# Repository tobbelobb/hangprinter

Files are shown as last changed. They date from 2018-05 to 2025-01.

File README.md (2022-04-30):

Hangprinter Hangprinter logo
===========

Welcome to the Hangprinter repository!

This branch contains Hangprinter version 4.
Breaking changes might occur from time to time.

For more general information about the Hangprinter Project, refer to [hangprinter.org](https://hangprinter.org).

Documentation
----------------
Start here: [hangprinter.org/doc/v4](https://hangprinter.org/doc/v4/).

Using letter sized paper for the layout?
-------------------------
You can specify that in a make-call:
```
make layout_letter.pdf
```

The `make` call will require Cairosvg, sed, and Ghostscript to work.
Already installed on many standard GNU/Linux systems.

Contributing Improvements
-------------------------
We're super grateful for merge request.
Please submit to this repo on Gitlab.

The second best option for contributing improvements is to make an issue on Gitlab.

Lead Dev
---------------------------------
[tobben](https://torbjornludvigsen.com).

Campaign
---------------------------------
[Github Sponsors](https://github.com/sponsors/tobbelobb/)

Merchandise
---------------------------------
[Spreadshirt link for Sweden](https://shop.spreadshirt.se/hangprinter-merchandise/).
[Spreadshirt link for US](https://shop.spreadshirt.com/hangprinter-merchandise/).

Credits
-------
See [contributors](https://gitlab.com/tobben/hangprinter/graphs/version_4) for committer stats.
Note that almost all ideas implemented by the commits have come up in conversations among fellow Reprappers.
Thanks!

List sorted alphabetically.

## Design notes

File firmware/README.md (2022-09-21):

## State of Hangprinter v4 firmware as of Sep 21, 2022

HP4 uses stock RepRapFirmware and ODrive firmware.

Read the the config files closely, they provide the most detail about how to use HP4 firmware.

## Changelog

### Sep 21, 2022
Latest stock ODrivefirmware (v0.5.5) is now used by HP4.
No more old or custom ODrive firmwares.

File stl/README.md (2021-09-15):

Make individual stls on your own by
 * Opening up the scad-files with OpenSCAD GUI and exporting from there

Or with `make`
 * `make stl/<thefileyouwant.stl>`
 * `make <thefileyouwant.stl>`,

... which will both place the stl inside the `hangprinter/stl/` directory.

Make all the stls on your own by
 * `make all` (this will take a long time),

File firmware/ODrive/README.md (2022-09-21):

## ODrive Usage On Hangprinter

Hangprinter uses stock ODrive Firmware version 0.5.5 or later.

Use a <a href="https://odriverobotics.com/shop/usb-isolator">USB isolator</a> between your laptop and your ODrive.

The source is kept here:
[https://github.com/madcowswe/ODrive](github.com/madcowswe/ODrive).

[The official ODrive docs](https://docs.odriverobotics.com/v/0.5.5/getting-started.html) are helpful in explaining many of the commands.

### How to Configure

Read every line of `configure_odrive.py`, including the comments manually before executing any of them.
Most of it can be copy/pasted in blocks, but in some places you have to wait.

I've included config dumps of my own ODrives here, and it might be tempting to use upload them directly to your own ODrives, like this

```
$ odrivetool restore-config odrive-config-AB.json  # With AB ODrive connected
$ odrivetool restore-config odrive-config-CD.json  # With CD ODrive connected
```

After those commands, you need to confirm that your break resistance matches the configured one.
You also need to do a calibration sequence and set a couple of variables:
odrivetool:
```
odrv0.config.brake_resistance = your_measured_value
odrv0.axis0.requested_state = AXIS_STATE_FULL_CALIBRATION_SEQUENCE
# wait...
odrv0.axis1.requested_state = AXIS_STATE_FULL_CALIBRATION_SEQUENCE
# wait...
odrv0.axis0.encoder.config.pre_calibrated = True
odrv0.axis1.encoder.config.pre_calibrated = True
odrv0.axis0.requested_state = AXIS_STATE_IDLE
odrv0.axis1.requested_state = AXIS_STATE_IDLE
odrv0.save_configuration()
# wait...
```

Also, the config backup does not include anti-cogging, so you have to set that up separately.
Look into `config_odrive.py` for how I set up anti-cogging.

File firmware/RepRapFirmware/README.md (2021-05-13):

The RepRapFirmware published here is to help those who intend to help develop it.
The final Hangprinter v4 Prototype 2 and onwards will use stock ReprapFirmware.

## Duet3 Firmware
Is under development, and development binaries will be uploaded here from time to time.
There are no guarantees here that the binaries uploaded here are tested, or will work
for you in any particular way.
Use only if you know what you're doing.

Stock ReprapFirmware, that will be part of Hangprinter long term, is developed here:
https://github.com/Duet3D/RepRapFirmware/

## Duet2 Firmware
This one was used by the Hangprinter 4 Prototype 1.
It used a Duet2 (Wifi) board and custom firmware.
It is deprecated and should not be used.
The source is kept here:
https://github.com/tobbelobb/RepRapFirmware/tree/v2-dev_hangprinter

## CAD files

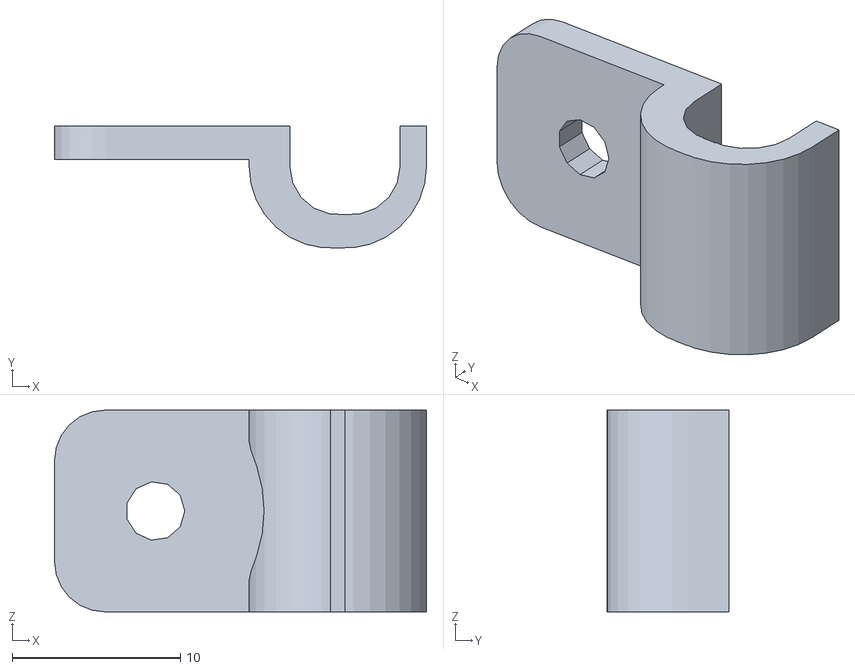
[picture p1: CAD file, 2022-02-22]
stl/cable_clamp_encoder_and_mains_cables.stl
22.1 x 7.27 x 12.0

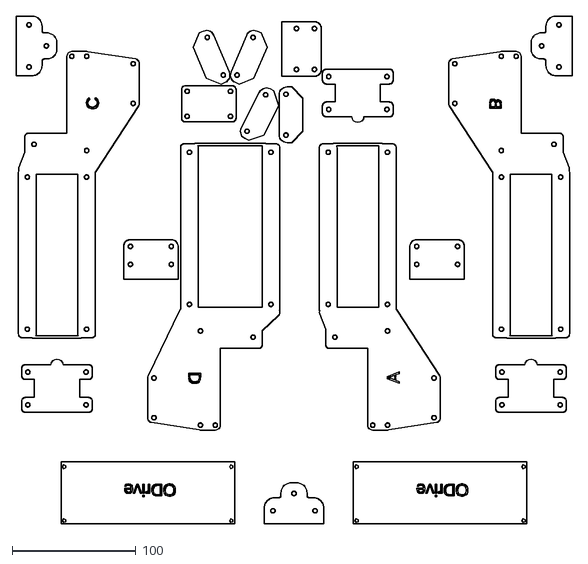
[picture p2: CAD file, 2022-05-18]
layout.dxf
448.7 x 409.7

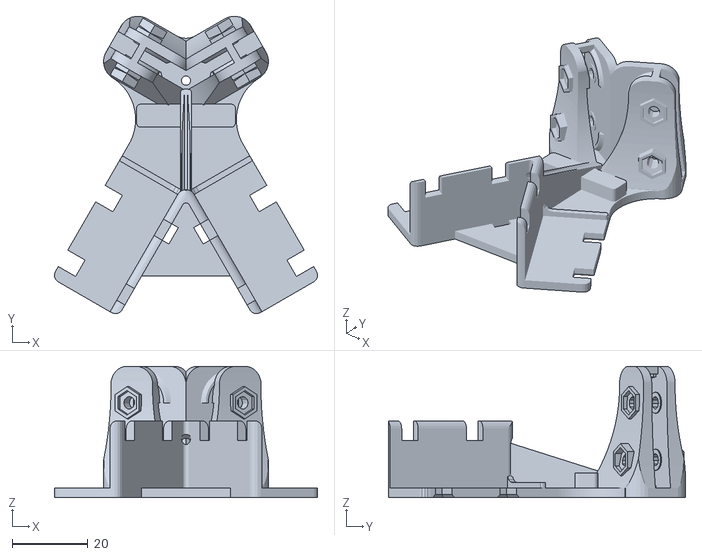
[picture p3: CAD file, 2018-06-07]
openscad_stl/corner_clamp.stl
69.2 x 78.3 x 34.6

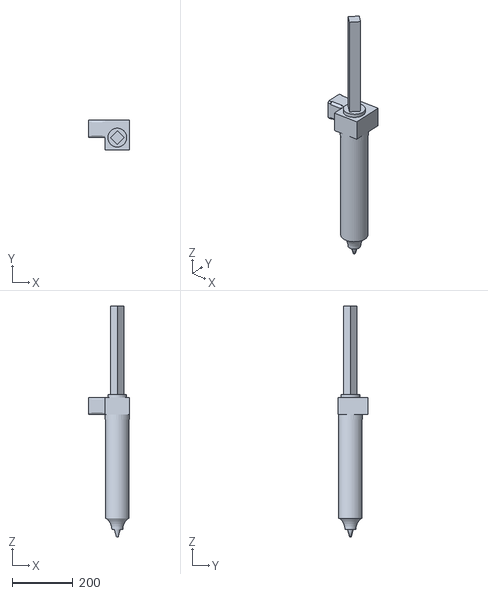
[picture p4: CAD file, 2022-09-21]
stl/for_render/ram_1000_3dpotter.stl
134.5 x 97.0 x 758.4

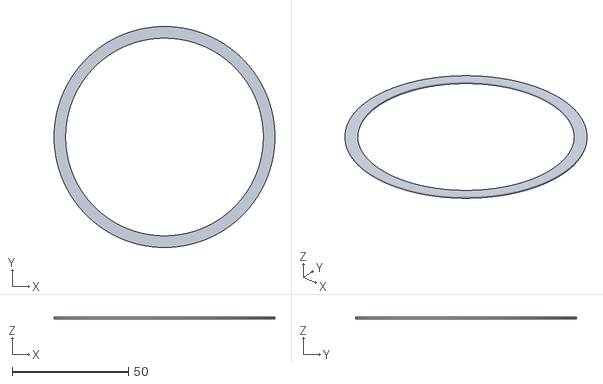
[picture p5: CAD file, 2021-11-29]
stl/hp-mark-markers/contrast_edge.stl
95.0 x 95.0 x 0.7

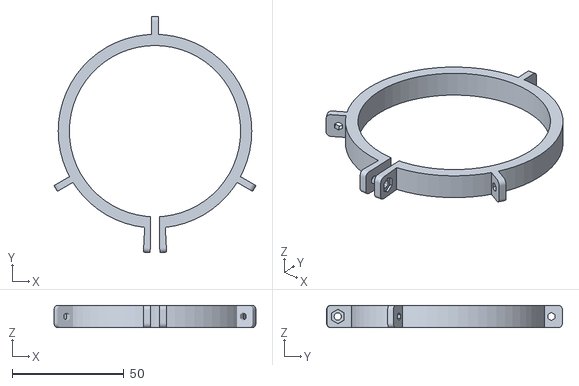
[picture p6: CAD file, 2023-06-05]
stl/ram_1000_3dpotter_holder.stl
90.4 x 105.6 x 10.0

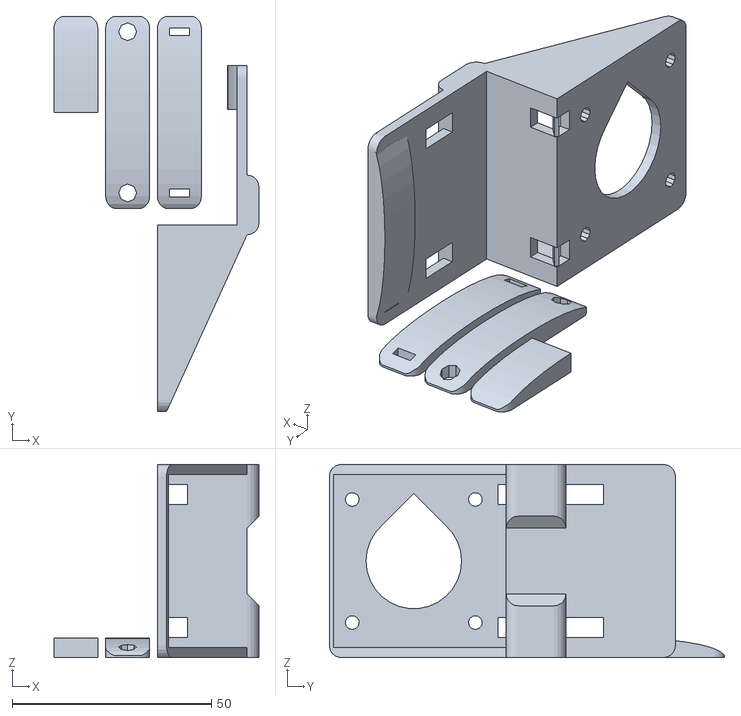
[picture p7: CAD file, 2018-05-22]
openscad_stl/extruder_holder.stl
51.5 x 99.3 x 48.5

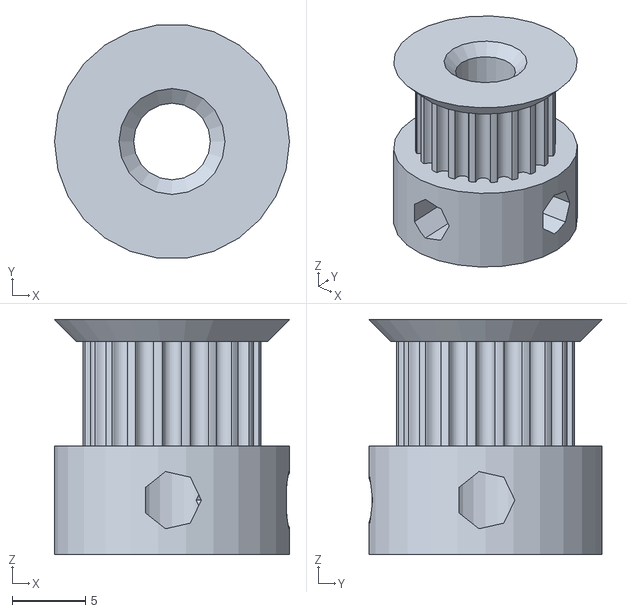
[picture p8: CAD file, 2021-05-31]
stl/for_render/GT2_motor_gear.stl
16.0 x 15.9 x 16.0

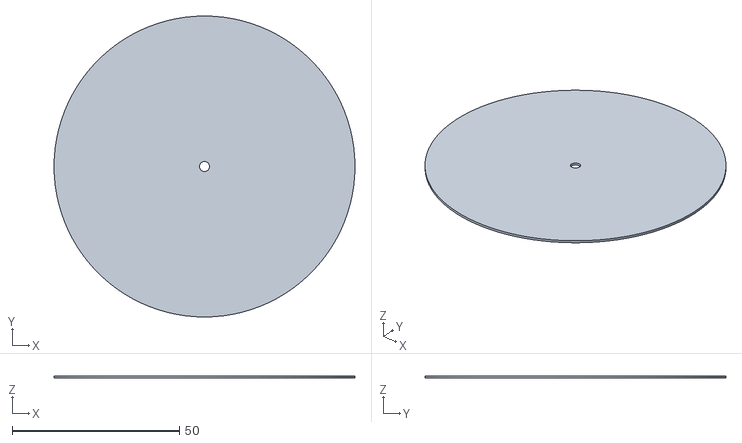
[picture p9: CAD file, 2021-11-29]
stl/hp-mark-markers/retroreflective_plate.stl
90.0 x 90.0 x 0.7

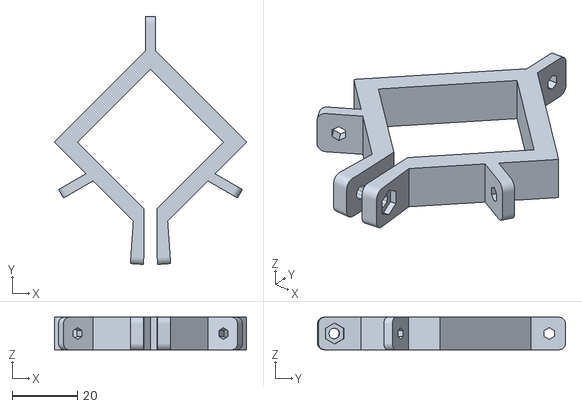
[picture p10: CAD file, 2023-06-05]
stl/ram_1000_3dpotter_top_holder.stl
59.0 x 76.1 x 10.0

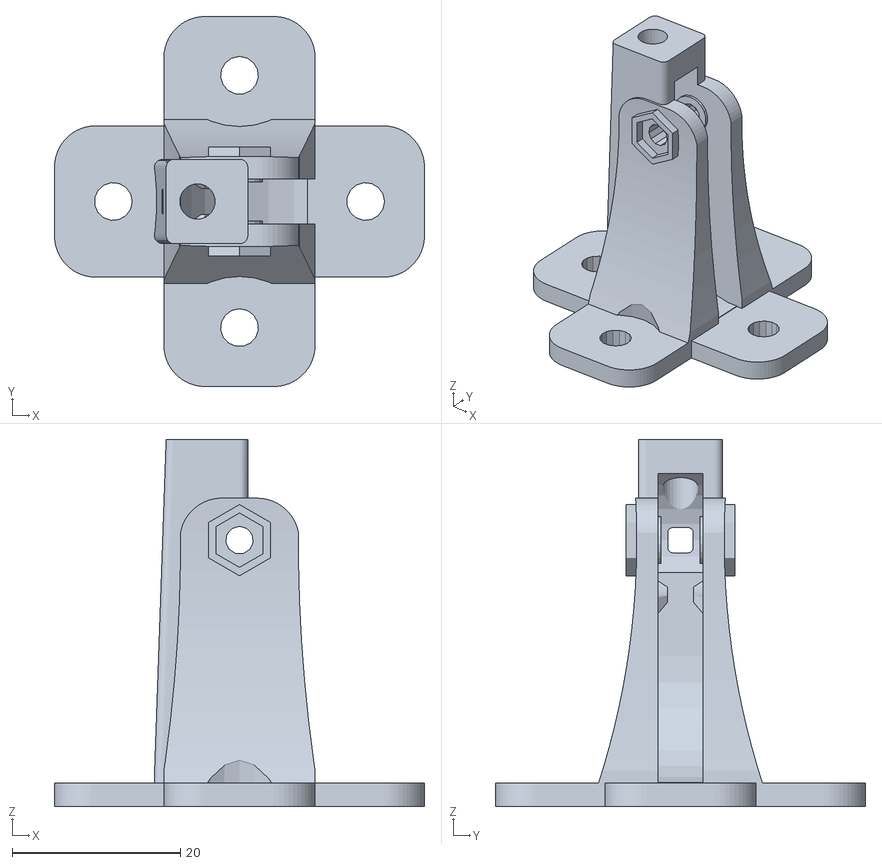
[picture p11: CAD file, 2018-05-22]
openscad_stl/lineroller_D.stl
44.0 x 44.0 x 43.7

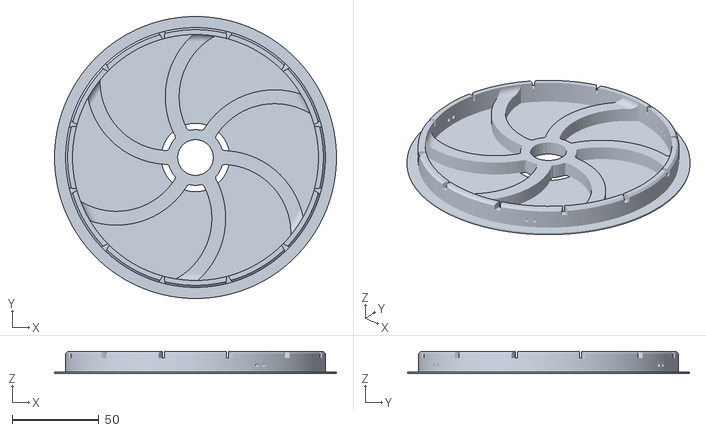
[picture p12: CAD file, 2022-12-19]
stl/dright_spool_top.stl
162.8 x 162.8 x 12.8

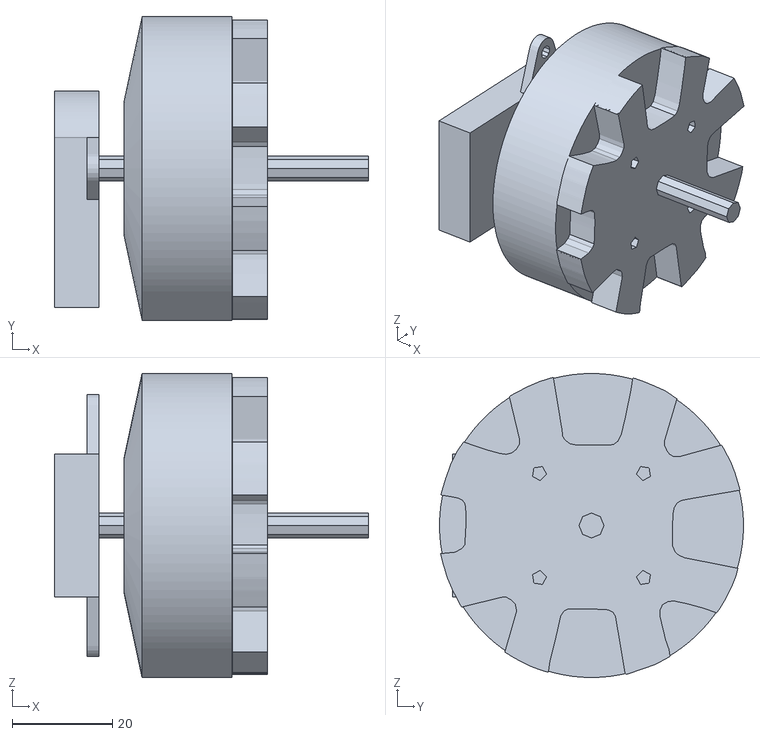
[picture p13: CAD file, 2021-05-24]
stl/for_render/whitelabel_motor.stl
62.8 x 60.8 x 60.8

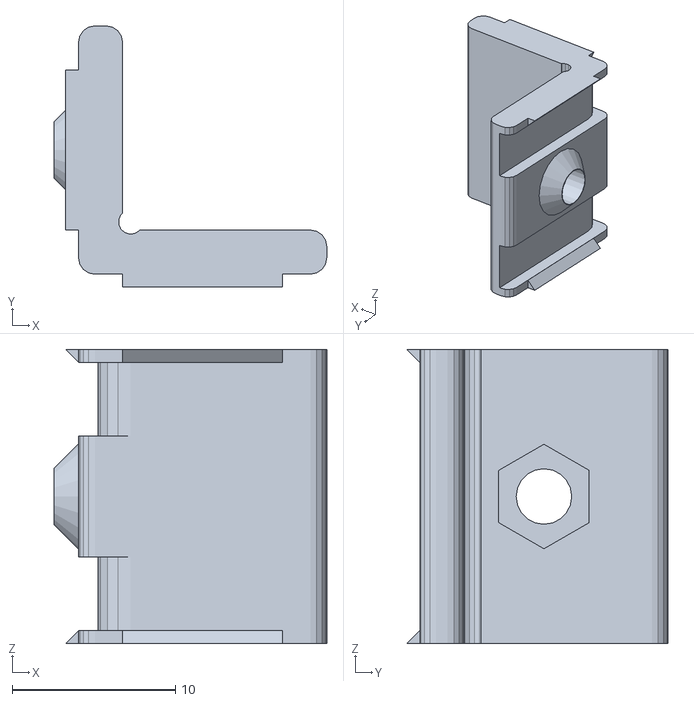
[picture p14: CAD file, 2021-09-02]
stl/hp-mark-markers/marker_slider.stl
16.7 x 16.0 x 18.0

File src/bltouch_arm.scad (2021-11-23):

include <lib/parameters.scad>
use <lib/util.scad>

//translate([-2.79-6,-4,2.5+145-42.65])
//  rotate([90,0,90])
//    %import("../stl/extruder_holder.stl");

//translate([0,0,-10.4-26.2-8-2])
//bltouch();
module bltouch(){
  cylinder(d=2, h=11);
  // The pin when fully stretched is 10.4 mm long
  translate([0,0,10.4])
    difference(){
      union(){
        translate([-12.61/2, 0, 0])
          cube([12.61, 12.61/2, 26.2]);
        cylinder(d=12.61, h=26.2);
        cylinder(d=10.7, h=26.2+8);
        translate([0,0,26.2+8]){
          for(k=[0,1]) mirror([k,0,0])
            linear_extrude(height=2)
              difference(){
                hull(){
                  translate([7.2/2, -10.6/2])
                    square([0.1, 10.6]);
                  translate([18/2, 0])
                    circle(r=3.65, $fn=6*4);
                }
                translate([18/2, 0])
                  circle(d=3.2);
              }
          translate([-7.2/2, -10.6/2])
            cube([7.2, 10.6, 2]);
        }
      }
      rotate_extrude()
        translate([9/2*sqrt(2)+7.5/2,-(9*sqrt(2))/2])
        rotate([0,0,45])
        square(9);
    }
}


rotate([90,0,0])
bltouch_arm(len = 98.5-14, rotit = false); // 98.5 - 14 works with my bondtech and supervolcano
module bltouch_arm(len = 98.5, rotit = false){
  difference(){
    translate([-8/2, 3.65, 0])
      rotate([90,0,0])
        ydir_rounded_cube2([8, len, 2*3.65], 3, $fn=6*4);
    for(k=[-1,1])
      translate([0,0,len+1.85-Nema17_cube_width/2+k*(Nema17_screw_hole_width/sqrt(2))/2])
        if (rotit)
          rotate([0,90,0]){
            cylinder(d=3.4, h=8, center=true, $fn=11);
            translate([0,0,-6.5])
              nut(5);
          }
        else
          rotate([90,0,0]){
            cylinder(d=3.4, h=8, center=true, $fn=11);
            translate([0,0,-6.5])
              nut(8);
          }
  }
  difference(){
    translate([-(19+2*3.65)/2, -3.65, 0])
      rounded_cube2([19+2*3.65, 2*3.65, 4], r=3.65, $fn=6*4);
    for(k=[0,1]) mirror([k,0,0])
      translate([18/2, 0, -1]){
        cylinder(d=3.3, h=6);
        translate([0,0,2.5])
          nut(5);
      }
  }
  for(k=[0,1]) mirror([k,0,0])
    translate([4,0,4])
      rotate([90,0,0])
        translate([0,0,-3.65])
          inner_round_corner(r=1.5, h=2*3.65, $fn=6*4);
}

// For use with flying pen braces
//rotate([90,0,0])
//bltouch_arm(len = 98.5 - 49, rotit = true);

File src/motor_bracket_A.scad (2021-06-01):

use <lib/whitelabel_motor.scad>

motor_bracket_A();
module motor_bracket_A(twod=false){
  mirror([1,0,0]) motor_bracket_extreme(leftHanded=false, twod=twod, "A");
}

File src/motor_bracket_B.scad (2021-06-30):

use <lib/whitelabel_motor.scad>

motor_bracket_B();
module motor_bracket_B(twod=false){
  mirror([1,0,0]) motor_bracket_extreme(leftHanded=true, twod=twod, text="B");
}

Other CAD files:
logo.dxf
openscad_stl/motor_gear.stl
stl/motor_bracket_B.stl
stl/motor_bracket_D.stl
src/motor_bracket_C.scad
Gear.scad
openscad_src/winch_layout.scad
src/1XD_holder.scad
src/GT2_spool_gear.scad
src/beam_slider_D.scad
src/bearing_u_608.scad
src/bearing_u_big_623.scad
src/belt_roller_insert.scad
src/brace_tightener.scad
src/cable_clamp.scad
src/clay_extruder.scad
src/corner_clamp.scad
src/dleft_spool.scad
src/dleft_spool_cover.scad
src/dright_spool_bottom.scad
src/dright_spool_cover.scad
src/dright_spool_top.scad
src/extruder_holder.scad
src/horizontal_line_deflector.scad
src/landing_brackets.scad
src/layout.scad
src/line_roller_anchor.scad
src/line_roller_anchor_template.scad
src/line_roller_wire_rewinder.scad
src/line_verticalizer.scad
src/motor_bracket_D.scad
src/new_tilted_line_deflector.scad
src/pen_fly_brace.scad
src/pen_holder_nut_head.scad
src/pi_mount.scad
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

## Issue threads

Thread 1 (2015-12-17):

can provide STL as an option ?

fred2088, 2015-12-17:

tobbelobb, 2015-12-17:
Did a set of renders, hope they're correct. Last number of their file names says how many you need to print. Use Hangprinter.scad for hints on how I intended to use them when I CADded them. Read blog http://vitana.se/opr3d/tbear/ for how they ended up being used.

Best of luck, let me know how its going for you.

Closed 2016-03-02.

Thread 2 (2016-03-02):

SCAD file missing

kartx22, 2016-03-02:
Hi some of the scad files are missing you did update #include .scad file but you didn't upload those files . can you upload those files?

tobbelobb, 2016-03-02:
Hi!
I'm unable to replicate your error. Which files and which branch?

Line 32 and 37 in Hangprinter.scad on the master-branch tries to import precompiled stl-files which aren't in the repo, that's all I can find. Removed them and pushed a commit so you don't have to search for them.

kartx22, 2016-03-09:
thanks

Closed 2016-03-09.

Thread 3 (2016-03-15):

square cable printer

kartx22, 2016-03-15:
Hi i would like to build a 3d printer with 4 corners can you give me some ideas?

tobbelobb, 2016-03-15:
With four corners, you could aim for a 5-axis machine.

kartx22, 2016-03-16:
ya, with this we can have access to the large scale printing with no limit.

Closed 2016-03-19.

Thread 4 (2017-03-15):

Closed Loop stepper motor

Tesla3DTore, 2017-03-15:
Hi,

Amazing JOB that your are doing until now!!! I would like to help you to improve your NEXT STEP of 3d printer that i'm sure will be the award of 2017!!!

You need a more precise stepper motor 16 or 32 step is not enought!!!
You need 256 step with a closed loop system so look at that project:

Wembi:
https://www.kickstarter.com/projects/109167261/wembi-closed-loop-motorupgrade-for-3d-printer?lang=fr

or

Mechaduino (open source):
https://github.com/jcchurch13

but for me a 32 bit controller with 256 microstepping is a must that you need to test so go here:
http://smoothieware.org/smoothieboard and look the V2 model (round shape ;-) )

I will print now your printer and add this features and give you feedback as soon as possible...

Best Regards,
Greg

tobbelobb, 2017-03-16:
Thanks!

Looking forwards to your contributions.

Closed 2017-03-16.

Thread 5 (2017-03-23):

Moving the movement steppers to the mounting points

twikis, 2017-03-23:
Hi Tobben!

Thank you very much for this amazing work, I just ordered the Vitamins for the printer and I'm going to print out the parts very soon.

Here's a thing: a few interested people and me are wondering why you haven't/aren't moving the movement steppers to the mounting points, in order to save weight on the printing head? This would save 600-750g (of course depending on the steppers used) on the print head, allowing for much higher accuracy, resolution, acceleration and speeds. The two simplest ways for doing this I can see are:
1. Taking the RAMPS out of the print head and putting it on the ground, then feeding the 8 stepper wires (D-Lines and extruder) +heater cartridge, fan and temperature sensor (maybe use a coax cable or amplifier to avoid interference) from the ground RAMPS to the print head and the stationary mounted steppers.
2. Leaving the RAMPS on the print head/moving it to a ground station and routing the stepper driver lines to dedicated stepper drivers mounted on a base station/the print head, depending on which version makes more sense. Pro: much less wires to take care off | Con: much more complicated

I understand that this will make the whole printer less compact and split it up in multiple parts, thereby making it less of a beauty, but I do think it's worth it when thinking about the speeds that could be archieved. Which is on the other hand making it much more attractive to everyone. How about a second brach for "enthusiasts"?

Alternatively you could of course gear down the motors for smaller stepper motors, as the rpm limit of steppers isn't even closely reached (unfortunately I don't have the skills to design this myself, otherwise I would).

Another thing we have come across: We've been thinking that much smaller motors may be sufficient for the D-Lines and extruder, thereby saving another few valuable grams. Could you provide any numbers regarding neccessary N/cm? Maybe by trying out how low you can go on current on the motors?

Greetings!

Matthias

PS. We've created a facebook group for the Hangprinter, you can find it here: https://www.facebook.com/groups/176856636157837

RigTig, 2017-03-23:
Matthias, there is a design (work-in-progress) using motors at the supports (see https://hackaday.io/project/13420-rigtigs-big-3d-printer) and it has been done several times before too. And the steppers are really light too. BUT, cabling is a pain especially when you want to adapt or move the support nodes. In fact, I started with cables to each node and found it far too awkward to set up each time, so I am now trying to use a local wifi network.
Besides, using long cables for high-current purposes is a poor design choice, made worse when you consider the effects from rapid off-on cycles (slower ramping speeds and power losses).

You said that you are:
> allowing for much higher accuracy, resolution, acceleration and speeds
but what accuracy, resolution, acceleration and speeds do you need when working at much greater scale than a desktop 3D printer. I've decided that for a 10 metre length of printing, a 2mm resolution is very acceptable (0.02%). And the speed needs to match the material being 'extruded'; note that clay can be pumped only so fast anyway. Assuming that accuracy refers to reproducibility, then the variation caused by the material is probably much higher than the effector location anyway. Anyway, this rant is really about choosing a desired outcome based on practicality rather than just pushing limits for the sake of pushing them.
If you or others are so keen on another branch, then just create a fork and go for it.

Tobben, I reckon you have achieved something quite amazing. Your whole printer fits into a bucket or backpack for transport and yet can print very large objects upon installation. Once I have finished this iteration of my own 3D printer, I am going to have a go at putting all the motors on the effector (as you have successfully done). I wish I had thought of it myself, since communicating with the remotely positioned motors has been the core of the issues with my approach. At least I have learnt a lot in the process of getting this far.

tobbelobb, 2017-03-23:
ABCD motors + RAMPS can be mounted in the ceiling (near the D-anchor points). Dynema lines can be routed such that firmware and worm drive can remain unchanged. Routing for A-lines would be like this:
D-anchor --> A-anchor --> A-action
An action point is a point where a line meets the moving unit.
All credz for this idea goes to Alexander Osika.

I strongly prefer constant length stepper cables.

Your comments and gearing down and downsizing motors are correct. Hangprinter in its current shape needs only ca 1 Ncm of torque. A Nema14 version should be possible, although less forgiving about pull from power cables and such.

Haha, the master branch is already for crazy enthusiasts. I'm still waiting for the first functional copy (other than my own) to appear. I'll make a branch as soon as I start developing a stationary-ABCD-motors version =)

RigTig: I'm really happy about any cross-pollination of our projects =)

twikis, 2017-03-23:
@RigTig Thank you for your answer, you're right I haven't read much about frameless printers other than the Hangprinter.
Thank you for explaining a bit about your printer!

Mate, I don't know why you're taking this personal or why you think it's necessary to play this up but so be it. Your rant is noted lol. I believe I've been respectful and don't care what you're making out of my suggestion to be honest.
Let's keep the positive spirit alive, okay?

Regarding reproducibility: What I mean are differences from one layer to another layer, those are just ruining every print. Same goes for wobble/ringing/ghosting and similar.
I agree with you that 2mm/10m accuracy are definitely sufficient.

And just think about it, wouldn't it be cool if the Hangprinter could also be used as a pretty good desktop 3D printer by only replacing the hotend? Just saying because I believe there's quite some potential in this.

@ Tobben thank you for your explanations! You mention that the Hangprinter needs less than 1 N/cm of force, so even the smallest NEMA14 should be enough and there are NEMA14s with 7 N/cm that weigh 50g. As the printer is becoming much lighter with lighter motors, even less is torque is needed as well. I believe the results could be worth it. Alternatively one could just use thicker dyneema lines, but that would also mean thicker spools... What diameter are you recommending/are you using by the way?

Alexander Osikas idea is great. The only drawback I can see is that the dynema lines will be a bit longer. Nice! Really looking forward to seeing qhat stationary ABCD version will be capable of.

I hope I can get it to work! Where do you think is the best place to post any questions and build notes so that other people can profit from them later on?

tobbelobb, 2017-03-23:
Sorry, the 1 Ncm was a brainfart. The motors need 15-20 Ncm in the current design. I've written about it [here](http://www.vitana.se/opr3d/tbear/2015.html#hangprinter_project_7) and [here](http://www.vitana.se/opr3d/tbear/#hangprinter_project_27)

Technical questions (that are not clearly bugs/issues with the design) are best posted here: forums.reprap.org/read.php?1,738858,758075
For build notes, choose whatever format you're comfortable with. Openbuilds, Hackaday and the RepRap wiki are all great.

Tesla3DTore, 2017-03-26:
Hi everybody,

Very good idea how to remove stepper to ground or ceil point...

https://youtu.be/sytyQvUXN8Q

So I thing a mix with that and the hangprinter will be the best..

I almost finish to print the part so I will be the first clone of hangprinter.. pictures and videos will follow for the end of this week...,

Closed 2017-03-26.

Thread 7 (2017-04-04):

Which file should I print?

batmanbat4, 2017-04-04:
should I print bottom_plate or Bottom_Plate2?

tobbelobb, 2017-04-04:
Oh, thanks for notifying. There's only supposed to be one bottom plate in the stl directory.

Bottom_plate_qty_1.stl is the "known to work" one. Bottom_plate2_qty_1.stl has slightly simplified (but untested) D-action points and no engraved letters.

I removed the old Bottom_plate_qty_1.stl. Only the untested one is left in the stl folder. It has changed name to Bottom_plate_qty_1.stl.

tobbelobb, 2017-04-04:
The answer to your question is: any of them is fine. :+1:

batmanbat4, 2017-04-04:
Thank you

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

Closed 2017-04-04.

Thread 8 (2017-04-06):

replacement part

batmanbat4, 2017-04-06:
hello, I was watching the interview with you and Thomas Sanladerer and you stated that you could replace the 2.7mm Eyes Inside Dia Fishing Rod Part with Bowden tubes.  I wanted to know how that could be done because I cannot seem to find the fishing rod part near me.
Thank you

tobbelobb, 2017-04-06:
Designing a PTFE eye wouldn't be hard, but then the ease of searching ebay has made me lazy (save some time). Search for example "2.8mm Dia Connector Ring" or "2.8mm Dia Fishing Rod Guide Repair Kit 5pcs" or similar...

If you can't wait for shipping, a pull request is most welcome!

Closed 2017-04-15.

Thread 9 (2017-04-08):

individual components in scad?

robssm, 2017-04-08:
Tobben,

I think perhaps the eyelet pillars on the botttom plate may benefit from some added ribs to increase the rigidity in some areas, maybe even the motor mounts also?

Can we get the scad for the bottom plate so it may be edited and reinforced?

I realize its all overkill, however, with the manner in which I am going to implement the hangprinter, this may become an issue ie in a heated enclosure.

tobbelobb, 2017-04-08:
Enforcing ribs is a good idea! The areas around the hole for the worm could also need some reinforcement.

An alternative way to reinforce is to control the level of infill. Modifiers in Slic3r is a good tool for that.

bottom_plate begins on line 158 in parts.scad
https://github.com/tobbelobb/hangprinter/blob/master/parts.scad#L158

Closed 2017-04-15.

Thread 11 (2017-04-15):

Bottom plate

jel111, 2017-04-15:
Having problems printing bottom plate. It staggers all the layers. i have printed everything else just fine. I am hoping you could take a look at that file for me. thanks John!

tobbelobb, 2017-04-15:
Take a look at your gcode (use http://gcode.ws/ or Slic3r or any tool you like). If you can't see staggering there, then the printer is the problem.

Example in Slic3r:
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

Closed 2017-06-21.

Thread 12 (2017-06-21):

Motor Drivers Dying

NikitiukPavel, 2017-06-21:
Hey! I've been trying to assemle your printer, but ran into one big issue. My motor drivers (DRV8825) constantly die.
I've tried cooling them with an extenal fan, which does prolong their lifecycle, but they still keep on dying on me.

How many amps do you send to the motors?
Can you give me any suggestions?

tobbelobb, 2017-06-21:
With so little info I can just guess that you don't tune your driver correctly, that you unplug motors while running, that your RAMPS is damaged or that something else is electrically wrong in your setup.

Try web search like for example:
https://duckduckgo.com/?q=DRV8825+dying+site%3Aforums.reprap.org

Or other relevant references like:
http://reprap.org/wiki/DRV8825
http://reprap.org/wiki/A4988_vs_DRV8825_Chinese_Stepper_Driver_Boards
https://www.pololu.com/product/2132/

Or if you need an intro to stepstick usage in general:
http://www.instructables.com/id/Drive-a-Stepper-Motor-with-an-Arduino-and-a-A4988-/

I'm closing since improving and debugging drv8825s is outside the scope of this repo.

Best regards

Closed 2017-06-21.

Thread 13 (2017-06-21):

Gear System Issue

NikitiukPavel, 2017-06-21:
Hey! There's also another issue I've ran into.

Should there be any additional holes in the sides of the gear for lace to go through? Cause I've made an additional hole in the side of the gear for that. Did I do it wrong?

Here are some photos of what I mean:
https://goo.gl/photos/LjXdNViA3kfSeRv28
https://goo.gl/photos/9uA4jrHUeYwvaGfo6

tobbelobb, 2017-06-21:
I connect all strings through the two holes included in the 3d model.

Your lines look a fair bit thicker than the ones I usually use though. See the facebook group for suggestions and discussions on specific types of lines: https://www.facebook.com/groups/hangprinter (one example here: https://www.facebook.com/groups/hangprinter/permalink/187803785063122/?match=bGluZXMsbGluZQ%3D%3D )

Closed 2017-07-17.

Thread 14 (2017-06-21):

Gear Movement issue

NikitiukPavel, 2017-06-21:
Another issue I've encountered is that Gear D (the most bottom one) move a little up and down, which makes it wobble on the sides. Currently I've hooked a washer to the gear above it to fix temopraly.

Is there a better solution to this problem?

tobbelobb, 2017-06-21:
I use grease on my worm, but still, mine wobbles a little as well. Hasn't been a problem though.

tobbelobb, 2017-06-21:
If I understand the issue right, then a par of large diameter thrust bearings would probably help?

Closed 2017-07-17.

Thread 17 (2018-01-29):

Issues Getting Files

JTonerII, 2018-01-29:
Hello,
I really like this project and would like to build it. However, I'm new to scad and when I try to copy/paste the lines of code into Open SCAD-->Preview or Render. I keep getting a Syntax Error. How do I successfully get these files to turn them into .stl files? Thank you,
JTonerII

tobbelobb, 2018-01-29:
There's no need to use OpenSCAD if you only want the standard Hangprinter parts.

The version 2 is on the master branch. It has stls in a directory called [stl](https://github.com/tobbelobb/hangprinter/tree/master/stl). Version 3 (which I recommend) is on the Openscad_version_3 branch. It has stls in a directory called [openscad_stl](https://github.com/tobbelobb/hangprinter/tree/Openscad_version_3/openscad_stl).

Copy/pasting code from the browser is not how Github is meant to be used. I cannot teach you git and Github here, but this is how you download the stls:
 * Go to the file you want to download.
 * Click it to view the contents within the GitHub UI.
 * In the top right, right click the Raw/Download button.
 * Save as.../Save link as...

tobbelobb, 2018-02-02:
The version 2 files all have a `qty_X.stl` ending to denote how many to print. The version 3 qtys are specified in the [bill of materials](https://github.com/tobbelobb/hangprinter/tree/Openscad_version_3#bill-of-materials).

Closed 2018-02-02.

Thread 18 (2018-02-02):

Uploads Are Disabled

JTonerII, 2018-02-02:
Not able to upload .stl files. Get a message that sat "Uploads are Disabled" "File Uploads Require Push Access to this Repository" Can the files be made to be uploadable, please? Thank you,   James

tobbelobb, 2018-02-03:
What files do you want to upload?

johnnyjeannatasha, 2023-08-13:
Unblock uploads

tobbelobb, 2023-08-14:
Sorry, this is a git repo, there's no such thing as unlock or upload.

You will need to clone the repo and make a push request. The Github repo is just a mirror, so I prefer pull requests (aka merge requests) to be submitted to the repo at Gitlab, here: https://gitlab.com/tobben/hangprinter

Closed 2018-02-09.

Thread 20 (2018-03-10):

Moving anchors - horizontal axes

DegenerateGroundState, 2018-03-10:
The hangprinter uses stationary anchors for the horizontal axes' lines and this means the build volume is constrained because of potential overlap, right? If instead the anchors move up (on rails perhaps) as the build platform moves up, the build volume would not decrease with height, correct?

I realize this would add significant cost and complexity, but it could be optional, depending on how much work this would take in software of course.

tobbelobb, 2018-03-11:
Yes, you are correct. When I printed the Babel Tower, I moved the ABC anchors on every printed meter and re-calibrated anchor positions. See my blog posts from Feb-March 2017 for details about that.

Closed 2018-03-11.

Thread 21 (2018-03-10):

Wire length feedback - Optical encoder?

DegenerateGroundState, 2018-03-10:
I watched the two build streams on the hangprinter on Thomas Sanladerer's channel and I remember hearing you have some repeatability issues when spooling/unspooling the wires, I'd go back and make sure but they're 10 hours put together! Have you considered using wires with a pattern on them combined with an optical encoder to close the loop on exactly how much you have on/off the spools?

davidelang, 2018-03-11:
where would you get such wires? and how fine could the pattern be?

I guess we could use it to check our assumptions about how many steps per cm if we had cm wide stripes on the wires.

but where can we buy thing (currently we are using fishing line)

DegenerateGroundState, 2018-03-11:
There are braided fishing lines made from multiple colors, and patterned fishing lines to hide the lines from fish (search camo fishing line). Best bet would probably be to go to a local tackle shop and ask, those that I have been to have been very knowledgeable. The trick would be finding one with a pattern that doesn't vary too much.
Also fishing line is tapered, perhaps you could use an optical encoder that senses width? Depends on how consistent the taper is and how expensive a suitable encoder would be.

You could also use a rotary encoder that is spun by the line through friction, though that would introduce slip again, but probably less than on a large spool.

DegenerateGroundState, 2018-03-11:
Neither solution would help with line stretch though, I guess you'd need an entirely separate encoder for that like a draw wire encoder, or could you measure how much the lines will stretch with a given load, derive a formula, and sense the current load on the line via a load cell?

nascimentohugo, 2018-03-11:
At Tom they mentioned fused lines (non-braided).
Also had issues trying to find it.
Only found at USA through eBay. And it's difficult to distinguish.
I bought both types but this one is thermal fused as they said middle video.
https://rover.ebay.com/rover/0/0/0?mpre=https%3A%2F%2Fwww.ebay.co.uk%2Fulk%2Fitm%2F221302781509
Berkley fireline thermally fused.
Nevertheless fused still gives some minor pattern

A Dom, 11 de mar de 2018, 07:30, Degenerate Ground State <
notifications@github.com> escreveu:

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
--

Hugo Nascimento, Arq.

urbanismo, arquitectura e fotografia | +351918945976
www.hugonascimento.com | fotografia
www.domusconcept.pt | director de arquitectura
www.adurbem.pt | colaborador
https://pt-pt.facebook.com/caminhada.att | co-fundador

davidelang, 2018-03-11:
If there is enough of a pattern (even if it is uneven), you can use something
like an optical mouse to track the movement.

an optical mouse is a camera with logic that watches for the picture to change.

with something as narrow as the lines, you may end up needing to put some sort
of lens in front of the mouse camera to magnify it's width.

As for line stretch/sag, rather than modeling it, measure it :-)

tobbelobb, 2018-03-11:
If you have bookmarks into the Tom's-streams, feel free to add them here: http://reprap.org/wiki/Links_Into_Hangprinter_v3_Build_Video

Line flex is repeatable, so the flex issue and the repeatability issue are separate. Two Bachelor's students here in Gothenburg (on of them called fredrudolf on RepRap forums) are working on both modelling flex and measuring mover position using computer vision. I derived some equations to help them with the flex model here: http://vitana.se/opr3d/tbear/2018.html#hangprinter_project_54 I do look forward to see them publishing, but we'll probably have to wait until June.

I guess that the repeatability issue I mentioned was related to how lines order themselves when rolled onto the spools. My approach so far has been to just increase spool radii and use thin lines. It works ok, but nothing more. When moving back and forth > 2 m, I typically see errors of 1-2 mm that are random, that I can't compensate with the current spools and doubled lines.

Note that there are two lines on each abc spool. They pick up different amounts of buildup error, so we can't solve the repeatability problem I'm talking about* without also changing the spools for something more complex. *(I call this problem "[the tilt problem](http://vitana.se/opr3d/tbear/2017.html#hangprinter_project_34)" on my blog, because it caused my v2 Hangprinter to tilt near top of tall prints.)

Adding encoders along the lines is something I've talked about a lot of times but never actually tested in hardware. I have a friend here in Gothenburg who has tested something similar, and he recommends a separate encoder roller with a pinching wheel to keep the line in place and to avoid slipping.

tobbelobb, 2018-03-11:
I think both load cells and optical encoders along the lines are good ideas. I did try to use force sensing resistors (FSRs) once: https://vitana.se/opr3d/tbear/2017.html#hangprinter_project_48 I recommend load cells over FSRs.

davidelang, 2018-03-11:
the mechanism used on older (non-optical) mice sounds like the right answer for
this. a small diameter roller with a wheel on it for the encoder.

joozn, 2018-03-12:
[Roll-up System.pdf](https://github.com/tobbelobb/hangprinter/files/1803284/Roll-up.System.pdf)
[spool_ring.pdf](https://github.com/tobbelobb/hangprinter/files/1803285/spool_ring.pdf)

- My idea for the repeatability issue would be to use a two roll system.
- the first spool the wire is rolled up on has a groove that runs around the spool, which through friction holds the wire and reels the wire in.
- because it gives off the line it doesn't build up.
- after that, there is a roll up roll that carries the excessive line.

joozn, 2018-03-12:
[wire clamping.pdf](https://github.com/tobbelobb/hangprinter/files/1803484/wire.clamping.pdf)
[system.pdf](https://github.com/tobbelobb/hangprinter/files/1803485/system.pdf)
some more fast schematics

tobbelobb, 2018-03-12:
Thanks joozn! I think the two roll system is also a good idea. Will you test it out in hardware? A weaver emailed me and suggested a similar concept. It is apparently how they do it on weaving machines. Some discussion in the fb group: https://www.facebook.com/torbjorn.ludvigsen/posts/319760511867448:15

joozn, 2018-03-13:
Yes, right now I am waiting for my new Prusa i3 mk3 to arrive, then I can start trying things out and prototyping. I will also build my first hangprinter then, might need some help.

Closed 2020-09-20.

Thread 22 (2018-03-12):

longer power outage while printing

potdian, 2018-03-12:
Hi there,

today I was in the Lab of disasterhack.org in Katmandu, Nepal and they are using your hangprinter to share knowledge about 3d-printing and to enable the locals to create innovative ideas.

Unfortunately there are a lot of power outages in Kathmandu and sometimes the UPS are not big enough to handle that interrupts and to keep the printing process alive.

So they are searching for a kind of restart the printing process at exact the last printed point. Is there a kind of write-ahead-log to log the last known position to sdcard, to re-read it a reboot and start printing at the last known position?

Any hints would be great!

Best regards
potdian

tobbelobb, 2018-03-13:
Hi potdian,
Cool that disasterhack has got their Hangprinter up!

You could connect 12V car/motorcycle battery if you increase your PSU voltage to ca 13.4V. See this video for details about how to increase PSU voltage:
https://www.youtube.com/watch?v=3U8ymhArTL4
and this thread for more discussion about using batteries:
forums.reprap.org/read.php?4,543092,543112

Some safetety features do exist in Marlin. I use this firmware:
https://github.com/tobbelobb/Marlin/tree/bugfix-1.1.x_hangprinter

The following procedure is very manual, but I have executed it a few times. I recommend reprap.org/wiki/Gcode if some of the gcodes are new to you.

The firmware linked above prints out current position (M114) at a quite high frequency during print. If there's a power outage I have at least some idea about where the printer was when it died. I can then search through the gcode text, and find the exact G1 command corresponding to that position. Putting that gcode into a gcode visualizer program, and comparing to the last lines that were actually printed, I can settle on exactly how much of the gcode was remaining when power was lost. I delete all the "used" gcode from the file, and save as "remaining.gcode" or something similar.

To restart print, I get to position using G6-moves, and use G92 to specify where the printer should think it is. Then I bring up hot end temperature manually. Then I load "remainin.gcode" and press print. I sometimes also create "remaining_no_extrusion.gcode", by removing all E-parameters from G1-commands. This lets me do some final G6-adjustments to make sure new layers end up exactly on top of the ones printed before the power outage.

Resuming SD prints manually is similar, except pronterface shows the last printed byte instead of the M114 position. You might get away with not creating "remaining.gcode". You can instead select SD file and select SD byte with special gcode commands before pressing print.

Many developers are currently focusing on creating more automated recoveries. RepRapFirmware (which has untested support for Hangprinter geometry) has [M911 and M916](http://reprap.org/wiki/GCodes#M911:_Configure_auto_save_on_loss_of_power). Also see M929: Start/stop event logging to SD card.

Anyway, since the Prusa MK3 has made a very good open source power outage recovery system, we will soon see something similar develop in Marlin. See for example discussion here: https://github.com/MarlinFirmware/Marlin/issues/9185

Best regards

potdian, 2018-03-15:
Thank you for your answer! I'll share it with diseasterhack and hopefully they can manage that.

Closed 2018-03-15.

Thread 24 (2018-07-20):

Missing lineroller_parameters.scad for 'make layout'

jdegenstein, 2018-07-20:
I noticed a (very minor) issue with creating the layout_letter.pdf. The lineroller_parameters.scad file appears to have been merged into parameters.scad. As a result of this, the command 'make layout_letter.pdf' fails.

Commenting out/deleting the appropriate lines in the Makefile appears to solve this issue, and the layout_letter.pdf is generated successfully. I believe the same issue applies to the other layout types, but I did not test it.

Just thought I would throw this out in case anyone has this issue.

tobbelobb, 2018-08-06:
Thanks for catching this and sorry for the late reply, I've been away on holidays.

I had also forgotten to remove references to 'gear_parameters.scad'. I pushed a fix on Gitlab: https://gitlab.com/tobben/hangprinter/commit/7600ec37a66ab559740eb81918174f655c3ed832

PS! Future development will be on Gitlab, I'll make a note in the Github Readme now ;)

Closed 2018-08-06.

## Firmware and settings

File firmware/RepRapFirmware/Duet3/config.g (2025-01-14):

; Communication and general
G21              ; Work in millimetres
G90              ; Send absolute coordinates...
M83              ; ...but relative extruder moves

; Kinematics
G4 S1                           ; Wait 1 second because expansion boards might not be ready to receive CAN signal yet.
M584 X40.0 Y41.0 Z42.0 U43.0 P4 ; map ABCD-axes to CAN addresses, and set four visible axes. Please excuse that ABCD motors are called XYZU here.
M584 E0:1:2:3:4:5               ; Regard all built in stepper drivers as extruder drives
M669 K6                         ; "This is a Hangprinter"
M669 P2000.0                    ; Printable radius (unused by Hangprinters for now)
M669 S430 T0.1                  ; Segments per second and min segment length

; Output of auto calibration script for Hangprinter
M669 A0.0:-1610.98:-131.53 B1314.22:1268.14:-121.28 C-1415.73:707.61:-121.82 D-0.00:0.01:2299.83
M666 Q0.08 R75.546:75.659:76.128:75.192
; Explanation:
; ; M669 defines the positions of the anchors, expressed as X:Y:Z distances between a line's pivot points, when the machine is homed.
; ; M666 sets Q=spool buildup, R=spool radii (incl buildup, when homed)

M208 Z2000.00  ; set maximum Z somewhere below D anchor. See M669 ... D<number>
M208 S1 Z-10.0 ; set minimum Z

; The following values must also be in the auto calibration script for Hangprinter (if you plan to use it)
M666 U2:2:2:4         ; Mechanical advantages on ABCD
M666 O1:1:1:1         ; Number of lines per spool
M666 L20:20:20:20     ; Motor gear teeth of ABCD axes
M666 H255:255:255:255 ; Spool gear teeth of ABCD axes

; Flex compensation
M666 W1.0                 ; Mover weighs 1 kg. Set to 0 to disable flex compensation.
M666 S20000.0             ; Spring constant (rough approximation) for Garda 1.1 mm line (unit N/m).
                          ; The real value is somewhere between 20k and 100k.
                          ; Lower value gives more flex compensation.
M666 I0.0:0.0:0.0:0.0     ; Min planned force in four directions (unit N).
                          ; This is a safety limit. Should affect only exceptional/wrong moves,
                          ; for example moves outside of the reachable volume.
M666 X70.0:70.0:70.0:70.0 ; Max planned force in four directions (unit N)
                          ; This is a safety limit. Will affect moves close to
                          ; the limits of the reachable volume.
M666 T10.0                ; Desired target force (unit N).
                          ; The flex compensation algorithm aims for at least
                          ; this amount of fource in the ABC line directions at all times.
                          ; It can be thought of as a minimum pre-tension value.
                          ; It's recommended to set it around 10 times higher
                          ; than your W (mover weight in kg) value.

; Guy wire lengths. Needed for flex compenation.
; Guy wires go between spool and final line roller.
; If your spools are all mounted on the D-anchor, on the ceiling plate, then you're all good,
; and you don't need to configure M666 Y values explicitly.
; If your spools are not all on the D-anchor then you must measure guy wire
; lengths and set them here.
; If your spools are all mounted on their respective anchors, so that you have no guy wires,
; then you should configure zeroed guy wire lengths M666 Y0.0:0.0:0.0:0.0.
;M666 Y-1.0:-1.0:-1.0:-1.0

; Torque constants. These are required for reading motor forces from ODrives
; They are the same values as is configured in the ODrives themselves (8.27/330 for motors in the standard  HP4 BOM)
;M666 C0.025061:0.025061:0.025061:0.025061

; Uncomment M564 S0 if you don't want G0/G1 moves to be be limited to a software defined volume
; M564 S0

; Drives
M666 J25:25:25:25 ; Full steps per ABCD motor revolution (match with ODrives...)

M569 P0 S1 ; Drive 0 goes forwards
M569 P1 S1 ; Drive 1 goes forwards
M569 P2 S1 ; Drive 2 goes forwards
M569 P3 S1 ; Drive 3 goes forwards
M569 P4 S1 ; Drive 4 goes forwards
M569 P5 S1 ; Drive 5 goes forwards

;; Warning: On a Hangprinter, ABCD motor directions shouldn't be changed, at least not
;;          via this config.g file.
;;          They are duplicated and hard coded into the firmware
;;          to make ODrive's torque mode go the right way.
;;          Please connect BLDC wires, from left to right, looking at the board
;;          from the front, so that ODrive silk screen is readable from left to right:
;;          |---------------------------------------------------------------|
;;          |DC                                                             |
;;          |-                    ODrive                                    |
;;          |+                                                              |
;;          |                          AUX                                  |
;;          |--||---||---||------------------------------------||---||---||-|
;;             ||   ||   ||                                    ||   ||   ||
;; ALT 1:   Black, Red, Blue                                Black, Red, Blue
;; ALT 2:  Yellow, Black, Red                              Yellow, Black, Red

M569 P40.0 S1 ; Drive 40.0 (A) goes forwards
M569 P41.0 S1 ; Drive 41.0 (B) goes forwards
M569 P42.0 S0 ; Drive 42.0 (C) goes backwards
M569 P43.0 S0 ; Drive 43.0 (D) goes backwards

; Speeds and accelerations
M201 X10000 Y10000 Z10000 U10000 E1000       ; Max accelerations (mm/s^2)
M203 X36000 Y36000 Z36000 E3600              ; Max speeds (mm/min)
M204 P2000 T4000                            ; Accelerations while printing and for travel moves
M566 X240 Y240 Z1200 E1200                 ; Maximum instant speed changes mm/minute

; Currents
M906 E1400 I60             ; Set motor currents (mA) and increase idle current to 60%

; Endstops
M574 X0 Y0 Z0                                ; set endstop configuration (no endstops)

; Thermistors and heaters
M308 S1 P"temp0" Y"thermistor" T100000 B3950 ; Configure sensor 1 as thermistor on temp1
M950 H1 C"out1" T1                           ; create nozzle heater output on out1 and map it to sensor 1
M307 H1 B0 S1.00                             ; disable bang-bang mode for nozzle heater and set PWM limit
M307 H1 A1271.9 C432.5 D8.2 V24              ; Set heater parameters (for Super Volcano 80W. You probably want to tune this yourself with M303.)
M143 H1 S280                                 ; set temp limit for nozzle heater to 280C
M570 S180                                    ; Hot end may be a little slow to heat up so allow it 180 seconds

; Fans
M950 F1 C"out7"
M106 P1 X255 T45 H1                                ; Enable Fan 1 thermostatic mode for sensor or heater 1 at 45 degrees
M950 F0 C"out8"                                    ; Defines a part cooling fan

; Find "temp0" and "out7" pins in the wiring diagram:
; https://duet3d.dozuki.com/Wiki/Duet_3_Mainboard_6HC_Wiring_Diagram

; Bltouch
; If you have a bltouch, see
; https://duet3d.dozuki.com/Wiki/Connecting_a_Z_probe#Section_BLTouch
; for how to install it
; Some of the commands below here might be different for you
; (eg if you don't have a Duet3 board, don't use the io7 headers, or have your bltouch mounted differently than me)
M950 S0 C"io7.out"
M558 P9 C"io7.in" H5 F120 T6000
G31 X15 Y27 Z8 P25 ; Measure these values in your own setup.

; These affect how you create and your mesh/grid bed compensation heightmap.csv values
; M557 X-200.001:200 Y-277.001:277 S80 ; Define a A2 sized grid with 1 cm margin...
; M376 H20 ; Taper the mesh bed compensation over 20 mm of z-height
; G29 S1 ; Load the default heightmap.csv and enable grid compensation


; Tool definitions
M563 P0 D0 H1                                      ; Tool number 0, with extruder drive 0 uses heater 1 and no fan
G10 P0 S0 R0                                       ; Set initial tool 0 active at standby temperature 0

; Miscellaneous
M92 E415                                           ; Set extruder steps per mm
M911 S10 R11 P"M913 X0 Y0 Z0 G91 M83 G1 Z3 E-5 F1000" ; set voltage thresholds and actions to run on power loss
T0                                                 ; Select tool 0

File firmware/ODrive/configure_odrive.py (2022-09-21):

# Use odrive-config-AB.json and odrive-config-CD.json to configure your ODrives:
# $ odrivetool restore-config odrive-config-AB.json
# Don't use this file to configure your ODrives, it's too error prone.
#
# Only use this file to help take notes and debug stuff if you're doing dev work
# on your ODrives.

# Hangprinter version 4's ODrives were originally roughly configured like described in this file

# These instructions have been update to roughly work for ODriveFirmware version 0.5.5.
# Some comments in here might help you if you use earlier versions as well.

#odrv0.config.brake_resistance = 0.4699999988079071 # Or 2.0. You need to check this with a multimeter

odrv0.config.enable_brake_resistor = True;
odrv0.axis0.controller.config.anticogging.anticogging_enabled = False
odrv0.axis1.controller.config.anticogging.anticogging_enabled = False

#odrv0.axis0.motor.config.pole_pairs = 7            # Default
#odrv0.axis0.controller.torque_setpoint = 0        # Default. Torque mode with zero torque

#odrv0.axis1.motor.config.pole_pairs = 7            # Default
#odrv0.axis1.controller.torque_setpoint = 0        # Default. Torque mode with zero torque

# At 58, the plastic parts start to vibrate badly
odrv0.axis0.controller.config.vel_limit = 40

odrv0.axis0.encoder.config.cpr = 8192     # AMT102-V
odrv0.axis0.motor.config.current_lim = 20 # Strong enough...
odrv0.axis0.motor.config.current_lim_margin=18
odrv0.axis0.motor.config.calibration_current = 20
odrv0.axis0.motor.config.torque_constant = 8.27/330

odrv0.axis1.controller.config.vel_limit = 58
odrv0.axis1.encoder.config.cpr = 8192     # AMT102-V
odrv0.axis1.motor.config.current_lim = 20 # Strong enough...
odrv0.axis1.motor.config.current_lim_margin=18
odrv0.axis1.motor.config.calibration_current = 20
odrv0.axis1.motor.config.torque_constant = 8.27/330

# PID tuning
odrv0.axis0.controller.config.pos_gain = 47
odrv0.axis0.controller.config.vel_integrator_gain = 0.2
odrv0.axis0.controller.config.vel_gain = 0.09

odrv0.axis1.controller.config.pos_gain = 47
odrv0.axis1.controller.config.vel_integrator_gain = 0.2
odrv0.axis1.controller.config.vel_gain = 0.09


# The AMT102-V has an index signal.
# See https://docs.odriverobotics.com/encoders#encoder-with-index-signal
odrv0.axis0.encoder.config.use_index = True
odrv0.axis1.encoder.config.use_index = True

odrv0.axis0.requested_state = AXIS_STATE_FULL_CALIBRATION_SEQUENCE
odrv0.axis1.requested_state = AXIS_STATE_FULL_CALIBRATION_SEQUENCE

odrv0.axis0.requested_state = AXIS_STATE_CLOSED_LOOP_CONTROL
odrv0.axis1.requested_state = AXIS_STATE_CLOSED_LOOP_CONTROL

odrv0.axis0.requested_state = AXIS_STATE_ENCODER_INDEX_SEARCH
odrv0.axis1.requested_state = AXIS_STATE_ENCODER_INDEX_SEARCH

odrv0.axis0.requested_state = AXIS_STATE_ENCODER_OFFSET_CALIBRATION
odrv0.axis1.requested_state = AXIS_STATE_ENCODER_OFFSET_CALIBRATION

odrv0.axis0.encoder.config.pre_calibrated = True
odrv0.axis0.config.startup_encoder_index_search = True
odrv0.axis0.motor.config.pre_calibrated = True
odrv0.axis1.encoder.config.pre_calibrated = True
odrv0.axis1.config.startup_encoder_index_search = True
odrv0.axis1.motor.config.pre_calibrated = True

# Have the same startup sequence automatically from now on
odrv0.axis0.config.startup_encoder_offset_calibration = False # True if you don't use encoder indexing
odrv0.axis0.config.startup_motor_calibration = False # True if you don't use encoder indexing
odrv0.axis0.config.startup_closed_loop_control = True

odrv0.axis1.config.startup_encoder_offset_calibration = False # True if you don't use encoder indexing
odrv0.axis1.config.startup_motor_calibration = False # True if you don't use encoder indexing
odrv0.axis1.config.startup_closed_loop_control = True

# Interface
#odrv0.config.enable_uart = False # before fw 0.5.2
odrv0.config.enable_uart_a = False # in fw 0.5.2 onwards

#odrv0.can.set_baud_rate(250000) # Default
odrv0.can.config.protocol = 1 # This changes to 0x1 somewhere between 0.5.1 and 0.5.4. So if you have an older firmware, it should be 0.
# odrv0.axis0.config.can.node_id = 40 # A. config.can_node_id in fw versions older than 0.5.2
# odrv0.axis1.config.can.node_id = 41 # B
# For the other board
odrv0.axis0.config.can.node_id = 42 # C
odrv0.axis1.config.can.node_id = 43 # D
odrv0.axis0.config.can.heartbeat_rate_ms = 0
odrv0.axis1.config.can.heartbeat_rate_ms = 0

odrv0.axis0.config.step_gpio_pin = 1
odrv0.axis0.config.dir_gpio_pin = 2
#odrv0.axis0.config.turns_per_step = 0.0025 # 1/(25*16) = 0.0025 # on older fw versions
odrv0.axis0.controller.config.circular_setpoints = False
odrv0.axis0.controller.config.circular_setpoint_range = 1
odrv0.axis0.controller.config.steps_per_circular_range = 400
odrv0.axis0.config.enable_step_dir = True
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

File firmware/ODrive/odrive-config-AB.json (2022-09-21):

{
  "axis0" : {
    "acim_estimator" : {"config" : {"slip_velocity" : 14.706000328063965}},
    "config" : {
      "dir_gpio_pin" : 2,
      "enable_sensorless_mode" : false,
      "enable_step_dir" : true,
      "enable_watchdog" : false,
      "startup_closed_loop_control" : true,
      "startup_encoder_index_search" : true,
      "startup_encoder_offset_calibration" : false,
      "startup_homing" : false,
      "startup_motor_calibration" : false,
      "step_dir_always_on" : false,
      "step_gpio_pin" : 1,
      "watchdog_timeout" : 0.0,
      "calibration_lockin" : {
        "accel" : 20.0,
        "current" : 10.0,
        "ramp_distance" : 3.1415927410125732,
        "ramp_time" : 0.4000000059604645,
        "vel" : 40.0
      },
      "can" : {
        "encoder_rate_ms" : 10,
        "heartbeat_rate_ms" : 0,
        "is_extended" : false,
        "node_id" : 40
      },
      "general_lockin" : {
        "accel" : 20.0,
        "current" : 10.0,
        "finish_distance" : 100.0,
        "finish_on_distance" : false,
        "finish_on_enc_idx" : false,
        "finish_on_vel" : false,
        "ramp_distance" : 3.1415927410125732,
        "ramp_time" : 0.4000000059604645,
        "vel" : 40.0
      },
      "sensorless_ramp" : {
        "accel" : 200.0,
        "current" : 10.0,
        "finish_distance" : 100.0,
        "finish_on_distance" : false,
        "finish_on_enc_idx" : false,
        "finish_on_vel" : true,
        "ramp_distance" : 3.1415927410125732,
        "ramp_time" : 0.4000000059604645,
        "vel" : 400.0
      }
    },
    "controller" : {
      "config" : {
        "axis_to_mirror" : 255,
        "circular_setpoint_range" : 1.0,
        "circular_setpoints" : false,
        "control_mode" : 3,
        "electrical_power_bandwidth" : 20.0,
        "enable_gain_scheduling" : false,
        "enable_overspeed_error" : true,
        "enable_torque_mode_vel_limit" : true,
        "enable_vel_limit" : true,
        "gain_scheduling_width" : 10.0,
        "homing_speed" : 0.25,
        "inertia" : 0.0,
        "input_filter_bandwidth" : 2.0,
        "input_mode" : 1,
        "load_encoder_axis" : 0,
        "mechanical_power_bandwidth" : 20.0,
        "mirror_ratio" : 1.0,
        "pos_gain" : 47.0,
        "spinout_electrical_power_threshold" : 10.0,
        "spinout_mechanical_power_threshold" : -10.0,
        "steps_per_circular_range" : 400,
        "torque_mirror_ratio" : 0.0,
        "torque_ramp_rate" : 0.009999999776482582,
        "vel_gain" : 0.09000000357627869,
        "vel_integrator_gain" : 0.20000000298023224,
        "vel_integrator_limit" : Infinity,
        "vel_limit" : 58.0,
        "vel_limit_tolerance" : 1.2000000476837158,
        "vel_ramp_rate" : 1.0,
        "anticogging" : {
          "anticogging_enabled" : false,
          "calib_anticogging" : false,
          "calib_pos_threshold" : 1.0,
          "calib_vel_threshold" : 1.0,
          "cogging_ratio" : 1.0,
          "index" : 0,
          "pre_calibrated" : false
        }
      }
    },
    "encoder" : {
      "config" : {
        "abs_spi_cs_gpio_pin" : 1,
        "bandwidth" : 1000.0,
        "calib_range" : 0.019999999552965164,
        "calib_scan_distance" : 50.26548385620117,
        "calib_scan_omega" : 12.566370964050293,
        "cpr" : 8192,
        "direction" : 1,
        "enable_phase_interpolation" : true,
        "find_idx_on_lockin_only" : false,
        "hall_polarity_calibrated" : false,
        "hall_polarity" : 0,
        "ignore_illegal_hall_state" : false,
        "index_offset" : 0.0,
        "mode" : 0,
        "phase_offset_float" : 0.56825852394104,
        "phase_offset" : 4229,
        "pre_calibrated" : false,
        "sincos_gpio_pin_cos" : 4,
        "sincos_gpio_pin_sin" : 3,
        "use_index_offset" : true,
        "use_index" : true
      }
    },
    "max_endstop" : {
      "config" : {
        "debounce_ms" : 50,
        "enabled" : false,
        "gpio_num" : 0,
        "is_active_high" : false,
        "offset" : 0.0
      }
    },
    "mechanical_brake" : {"config" : {"gpio_num" : 0, "is_active_low" : true}},
    "min_endstop" : {
      "config" : {
        "debounce_ms" : 50,
        "enabled" : false,
        "gpio_num" : 0,
        "is_active_high" : false,
        "offset" : 0.0
      }
    },
    "motor" : {
      "config" : {
        "I_bus_hard_max" : Infinity,
        "I_bus_hard_min" : -Infinity,
        "I_leak_max" : 0.10000000149011612,
        "R_wL_FF_enable" : false,
        "acim_autoflux_attack_gain" : 10.0,
        "acim_autoflux_decay_gain" : 1.0,
        "acim_autoflux_enable" : false,
        "acim_autoflux_min_Id" : 10.0,
        "acim_gain_min_flux" : 10.0,
        "bEMF_FF_enable" : false,
        "calibration_current" : 20.0,
        "current_control_bandwidth" : 1000.0,
        "current_lim_margin" : 18.0,
        "current_lim" : 20.0,
        "dc_calib_tau" : 0.20000000298023224,
        "inverter_temp_limit_lower" : 100.0,
        "inverter_temp_limit_upper" : 120.0,
        "motor_type" : 0,
        "phase_inductance" : 2.3265618438017555e-05,
        "phase_resistance" : 0.03775078058242798,
        "pole_pairs" : 7,
        "pre_calibrated" : false,
        "requested_current_range" : 60.0,
        "resistance_calib_max_voltage" : 2.0,
        "torque_constant" : 0.025060605257749557,
        "torque_lim" : Infinity
      },
      "fet_thermistor" : {
        "config" : {
          "enabled" : true,
          "temp_limit_lower" : 100.0,
          "temp_limit_upper" : 120.0
        }
      },
      "motor_thermistor" : {
        "config" : {
          "enabled" : false,
          "gpio_pin" : 4,
          "poly_coefficient_0" : 0.0,
          "poly_coefficient_1" : 0.0,
          "poly_coefficient_2" : 0.0,
          "poly_coefficient_3" : 0.0,
          "temp_limit_lower" : 100.0,
          "temp_limit_upper" : 120.0
        }
      }
    },
    "sensorless_estimator" : {
      "config" : {
        "observer_gain" : 1000.0,
        "pll_bandwidth" : 1000.0,
        "pm_flux_linkage" : 0.0015800000401213765
      }
    },
    "trap_traj" : {
      "config" : {"accel_limit" : 0.5, "decel_limit" : 0.5, "vel_limit" : 2.0}
    }
  },
            "axis1"
      : {
        "acim_estimator" : {"config" : {"slip_velocity" : 14.706000328063965}},
        "config" : {
          "dir_gpio_pin" : 8,
          "enable_sensorless_mode" : false,
          "enable_step_dir" : true,
          "enable_watchdog" : false,
          "startup_closed_loop_control" : true,
          "startup_encoder_index_search" : true,
          "startup_encoder_offset_calibration" : false,
          "startup_homing" : false,
          "startup_motor_calibration" : false,
          "step_dir_always_on" : false,
          "step_gpio_pin" : 7,
          "watchdog_timeout" : 0.0,
          "calibration_lockin" : {
            "accel" : 20.0,
            "current" : 10.0,
            "ramp_distance" : 3.1415927410125732,
            "ramp_time" : 0.4000000059604645,
            "vel" : 40.0
          },
          "can" : {
            "encoder_rate_ms" : 10,
            "heartbeat_rate_ms" : 0,
            "is_extended" : false,
            "node_id" : 41
          },
          "general_lockin" : {
            "accel" : 20.0,
            "current" : 10.0,
            "finish_distance" : 100.0,
            "finish_on_distance" : false,
            "finish_on_enc_idx" : false,
            "finish_on_vel" : false,
            "ramp_distance" : 3.1415927410125732,
            "ramp_time" : 0.4000000059604645,
            "vel" : 40.0
          },
          "sensorless_ramp" : {
            "accel" : 200.0,
            "current" : 10.0,
            "finish_distance" : 100.0,
            "finish_on_distance" : false,
            "finish_on_enc_idx" : false,
            "finish_on_vel" : true,
            "ramp_distance" : 3.1415927410125732,
            "ramp_time" : 0.4000000059604645,
            "vel" : 400.0
          }
        },
        "controller" : {
          "config" : {
            "axis_to_mirror" : 255,
            "circular_setpoint_range" : 1.0,
            "circular_setpoints" : false,
            "control_mode" : 3,
            "electrical_power_bandwidth" : 20.0,
            "enable_gain_scheduling" : false,
            "enable_overspeed_error" : true,
            "enable_torque_mode_vel_limit" : true,
            "enable_vel_limit" : true,
            "gain_scheduling_width" : 10.0,
            "homing_speed" : 0.25,
            "inertia" : 0.0,
            "input_filter_bandwidth" : 2.0,
            "input_mode" : 1,
            "load_encoder_axis" : 1,
            "mechanical_power_bandwidth" : 20.0,
            "mirror_ratio" : 1.0,
            "pos_gain" : 47.0,
            "spinout_electrical_power_threshold" : 10.0,
            "spinout_mechanical_power_threshold" : -10.0,
            "steps_per_circular_range" : 400,
            "torque_mirror_ratio" : 0.0,
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

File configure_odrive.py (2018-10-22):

# This is meant for resetting A-motor if its oDrive settings get erased
# Could also speed up configuration of the other motors considerably

import odrive
odrv0 = odrive.find_any()

# 4500 rpm specced here:
# https://docs.google.com/spreadsheets/d/1OBDwYrBb5zUPZLrhL98ezZbg94tUsZcdTuwiVNgVqpU/edit#gid=0
# (4500/60)*2400 = 180000
#odrv0.axis0.controller.config.vel_limit = 180000
# At 140000 the plastic parts starts to resonate
odrv0.axis0.controller.config.vel_limit = 130000
odrv0.axis0.motor.config.calibration_current = 10 # Default
odrv0.config.brake_resistance = 0.4699999988079071 # Default
odrv0.axis0.motor.config.pole_pairs = 7 # Default
odrv0.axis0.encoder.config.cpr = 2400 # Generic 600 ppr optical encoder
odrv0.axis0.motor.config.current_lim = 30 # Strong enough...
odrv0.axis0.controller.current_setpoint = 0 # Default. Torque mode with zero torque

# Enforce startup sequence this time
odrv0.axis0.requested_state = AXIS_STATE_FULL_CALIBRATION_SEQUENCE
# Wait for calibration to finish...
while my_drive.axis0.current_state != AXIS_STATE_IDLE:
    time.sleep(0.1)
odrv0.axis0.requested_state = AXIS_STATE_CLOSED_LOOP_CONTROL

# Have the same startup sequence automatically from now on
odrv0.axis0.config.startup_encoder_offset_calibration = True
odrv0.axis0.config.startup_closed_loop_control = True
odrv0.axis0.config.startup_motor_calibration = True

# PID tuning
odrv0.axis0.controller.config.pos_gain = 70
odrv0.axis0.controller.config.vel_integrator_gain = 0.002
odrv0.axis0.controller.config.vel_gain = 0.0045

# Interface
odrv0.config.enable_uart = True
odrv0.axis0.config.enable_step_dir = True
odrv0.axis0.config.counts_per_step = 0.75 # 2400/(200*16) = 0.75

odrv0.save_configuration()
odrv0.reboot()

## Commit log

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2015-06-01 Completely reorganized code separating placement modules, render modules and modules to be printed.
    [Gears.scad, Hangprinter.scad, Nema17_and_Ramps_and_bearings.scad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]
2015-06-01 In the middle of changing extruder motor so it protrudes up through bottom_plate
    [Gears.scad, Hangprinter.scad, design_numbers.scad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]
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2015-06-15 Placed lines using design parameters resembling the ones used in Marlin (hard-coded action point coordinates)
    [Gears.scad, design_numbers.scad, parts.scad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]
2015-06-15 Made frames use parameterized coordinates and sketchet up a fish ring module
    [parts.scad, placed_parts.scad, util.scad]
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2015-07-04 Minor adjustments to bottom_plate to ease build. Making better place for screw heads etc.
    [design_numbers.scad, measured_numbers.scad, parts.scad]
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2015-09-16 Used nop for widening step pulses, final configuration before first dry run
    [Configuration.h]
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2015-09-21 Gave one of sandwich gear's teeth to motor gear instead, ca 10% force gain
    [design_numbers.scad]
2015-09-21 Fixed sqrt of negative-bug in tangent-functions
    [util.scad]
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2015-09-21 Shortened motor gear c to make place for line.
    [Gears.scad, design_numbers.scad, placed_parts.scad]
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2015-11-13 Made mount for e3d v6. Observe: Extruder_motor_twist value in design_numbers.scad is changed, so bottom_plate is changed.
    [Hangprinter.scad, design_numbers.scad, parts.scad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]
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2015-11-17 Noted that Marlin is not original version. Removed non-relevant files from original Marlin repo.
    Conflicts:
    firmware/test_binary_search.c
    placed_parts.scad
    [Marlin Logo.dxf, Menu Plans.xlsx]
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2015-12-03 Fixed alignment issue of hot end entrance
    [design_numbers.scad, measured_numbers.scad, parts.scad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]
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2015-12-17 Made complete render, found some bugs
    [Gears.scad, design_numbers.scad, parts.scad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]
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2016-11-16 Shorter worm that renders more easily
    [Gears.scad, Nema17_and_Ramps_and_bearings.scad, design_numbers.scad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]
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2016-11-17 Left more material around worm for bottom plate stiffness
    [parts.scad]
2016-11-17 Re-fixed issue with E-motor hitting sandwich
    [design_numbers.scad, parts.scad]
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2016-11-18 Moved abc towers closer to each other to prevent d lines hitting A-towers
    [design_numbers.scad]
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2016-11-29 Stepper weight corrected
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2016-11-29 Correct placed_lines
    [placed_parts.scad]
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2016-12-05 Fix Sstruder hot end mount groove
    [design_numbers.scad, parts.scad]
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2016-12-07 Fix Sstruder bugs
    [parts.scad]
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2016-12-11 Corrected update_steps_per_unit
    [Configuration.h]
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2016-12-14 Fix bug in update_axis_steps_per_unit
    [Configuration.h]
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2017-01-13 Fixed bug in Sstruder_plate.stl
    [Sstruder_plate_qty_1.stl]
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2017-01-27 Assure correct usage of axis_steps_per_unit
    [Configuration.h]
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2017-02-02 Add missing se3_exp_2
    [sweep.scad]
2017-02-02 Add missing function so3_exp_2
    [sweep.scad]
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2017-03-27 Strengthen motor gear A shaft
    [Gears.scad, design_numbers.scad]
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2017-04-03 Add a supporting axle to the worm gear
    Also hollow out the frame to allow this axle
    [Gears.scad, design_numbers.scad, parts.scad]
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2017-04-14 Generate Top_plater_qty_1.stl
    It looks like the top plate was missing from the generated stl folder.
    [Top_plate_qty_1.stl]
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2017-04-21 Strengthens weakest bottom_plate extrema
    [parts.scad]
2017-04-21 Adds stl of bottom_plate with strengthened weakest extrema
    [Bottom_plate_qty_1.stl]
2017-04-21 Fixes bpr bug and splits enforcement of weakest extrema
    [parts.scad]
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2017-07-26 Fixes G7 and prints out proper angle
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2017-08-27 - fixed D (E1) Motor direction issue
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2017-09-25 Fixes non-manifold lineroller_D export
    [lineroller_D.scad, lineroller_anchor.scad]
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2017-09-29 Fixes lineroller bugs
    [lineroller_ABC_winch.scad, lineroller_D.scad, lineroller_anchor.scad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]
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2017-09-29 Shortens lineroller at anchor
    [lineroller_ABC_winch.scad, lineroller_anchor.scad]
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2017-09-30 Fixes diameter of 608 bearing
    [gear_util.scad, parameters.scad, spool.scad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]
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2017-11-08 Gives 1 mm more clearing between large gear and plywood. Also fixes some bugs in lineroller scad code.
    [gear_parameters.scad, layout.scad, lineroller_ABC_winch.scad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]
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2017-11-19 Makes G95 do only tightening, never loosening
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2018-01-03 Stiffens corner extrema
    [corner_clamp.scad, corner_clamp.stl]
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2018-01-24 Fixes direction of torque mode
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2018-02-06 Rewrites encoder reading and moves it from "G97 A B C D" to "M114 S1"
    [Configuration.h]
2018-02-06 Makes possible to take into account a flipped motor connector when reading Mechaduino encoder
    [Configuration.h]
2018-02-09 Stiffens up motor bracket
    [motor_bracket.scad, motor_bracket.stl]
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2018-02-09 Fixes M3 screw qtys
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2018-02-12 Fixes bug in beam sliders' namings
    [beam_slider_ABC.scad, beam_slider_D.scad]
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2018-02-12 Adds spool shaft to attach with wood screws and wood screw layout dxf
    [gear_parameters.scad, gear_util.scad, layout.dxf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]
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2018-02-14 Makes motor_gear 3 mm narrower, spool radius 5 mm larger, makes sandwich easier to separate and saves some plastic
    [gear_parameters.scad, gear_util.scad, layout.dxf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]
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2018-02-14 Fix typos
    [layout.scad]
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2018-02-28 Shortens spool core so washer can be used to pinch 608 bearings
    [spool_core.scad, spool_core.stl]
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2018-03-05 Fixes bugs in layout
    [layout.dxf, layout.scad]
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2018-03-15 Replaces big wall sweep with cube/cylinder diff
    [lineroller_ABC_winch.scad, lineroller_anchor.scad]
2018-03-15 Replaces small sweep with partial rotate_extrude
    [lineroller_ABC_winch.scad]
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2018-05-21 Stiffens up motor brackets
    [motor_bracket.scad, motor_bracket.stl, util.scad]
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2018-05-22 Squashed 'firmware/Mechaduino_subtree/' changes from 09a5fab..30d9a5b
    30d9a5b Reads encoder to sit still on startup
    e2bc136 Lowers PA to aps*0.7
    e54516f Removes crazy jerky/reverse motion bug
    b8218b4 Fixes indentation and style and removes default lookup table
    git-subtree-split: 30d9a5b35cf02a0d297537b87b77612d6c1d9701
    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
2018-06-07 Gives line and bearings more room in corner clamp, and makes corner clamp stiffer.
    [corner_clamp.scad, corner_clamp.stl]
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2018-09-17 Removes non-flat bottom bug
    [donkey_bracket.scad]
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2018-10-04 Adds some more ceiling unit line routing and bug fixes
    [layout.scad, line_roller_ABC_winch.scad, line_roller_D_winch.scad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]
2018-10-05 Rewrites line rollers and fixes some bugs in them
    [GT2_spool_gear.scad, belt_roller.scad, belt_roller.stl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]
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2018-10-09 Gives spacer a fixed fn
    [util.scad]
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2018-10-09 Fixes import bugs
    [layout.scad]
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2018-10-10 Fixes lineroller rendering module
    [layout.scad]
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2018-10-11 Flips GT2 motor gear and shrinks donkey bracket to make more compact drives
    [donkey.scad, donkey.stl, donkey_bracket.scad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]
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2018-10-12 Flips GT2 motor gear back, separates Donkey and encoder more, and separates spools more. Everything to give motor/encoder pairs more space.
    [donkey.scad, donkey_bracket.scad, layout.dxf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]
2018-10-12 Fixes cable clamp
    [cable_clamp.scad]
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2018-10-15 Makes some more space to roll in that D bearing in corner clamp
    [corner_clamp.scad]
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2019-01-04 Fixes typos in RRF default config
    [config.g]
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2019-05-12 Specifies dependencies correctly
    [spool_core.scad]
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2019-05-27 Adds line collision check for cylinder prints
    - The method requires that the model can be abstracted
    down to a series of closed paths along outer perimeter
    of each layer.
    [simplified_print_volume_verification.scad]
2019-05-27 Fixes comments
    [simplified_print_volume_verification.scad]
2020-07-22 Moves step/dir from pin 5/6 to pin 1/2
    This fixes problems with noise on the dir pin.
    UART is moved to GPIO 3/4, and firmware is on a branch of the upstream ODrive repo:
    https://github.com/madcowswe/ODrive/tree/usart2
    [configure_odrive.py]
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2021-05-03 Adds landing_bracket to 2d layout.pdf
    Also encapsulates mounting screw 2d shape into the module
    [donkey_bracket.scad, horizontal_line_deflector.scad, landing_bracket.scad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]
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2021-05-07 Adds a bracket for 1XD expansion boards
    The 1XD boards will not be part of the final HP4,
    but we have to live with them for at least three months or so.
    During that time we will accept them for the sake of being
    able to develop and test RepRapFirmware freely
    [1XD_holder.scad]
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2021-05-20 Melts together belt roller and motor bracket
    [belt_roller.scad, parameters.scad, util.scad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]
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2021-05-24 Brings belt roller 2 mm closer to motor
    This reduces torque across the motor shaft.
    Also places belt roller along x=0 plane,
    to make it easier to align belt paths in layout.scad.
    [motor_bracket.stl, whitelabel_motor.scad]
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2021-05-25 Increases spool radius
    ... as well as many other little adjustments for the HP4 prototype 2
    [GT2_spool_gear.scad, dleft_spool.stl, horizontal_line_deflector.scad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]
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2021-05-27 Fixes BC line placements
    [layout.scad]
2021-05-31 Removes line length tuner hook
    We don't need it because we can use a simlpe screw that's attached to
    the wooden plate instead.
    [line_length_tuner_hook.scad, line_length_tuner_hook.stl]
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2021-06-01 Prepares hole for brace tightener screw
    [corner_clamp.scad, corner_clamp.stl]
2021-06-01 Adds nutlock to brace tightener
    [brace_tightener.scad, brace_tightener.stl]
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2021-06-02 Fixes bug in corner clamp
    Walls that hold ABC bearings were packed to tight together
    [corner_clamp.scad, corner_clamp.stl]
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2021-06-02 Fixes yet another bug on the corner clamp
    [corner_clamp.scad, corner_clamp.stl]
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2021-06-03 Fixes some minor bugs
    [corner_clamp.scad, corner_clamp.stl, layout.dxf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]
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2021-06-03 Cosmetic fix
    [corner_clamp.scad, corner_clamp.stl]
2021-06-03 Fixes the spool cover via Blender...
    Prusa Slicer just refuses to put the layers where I want them otherwise
    [spool_core.scad, spool_cover.scad, spool_cover.stl]
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2021-06-04 Increases bearing shoulder height in spool cover
    Also places BC sandwiches as close to plate's edge as possible.
    [dleft_spool_cover.scad, dleft_spool_cover.stl, layout.dxf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]
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2021-06-07 Fixes spool cover stl
    [spool_cover.stl]
2021-06-07 Fixes dleft spool cover
    [dleft_spool_cover.stl]
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2021-06-09 Gives bearing and screw head some more space
    ... in the three deflectors
    [horizontal_line_deflector.stl, tilted_line_deflector.scad, tilted_line_deflector.stl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]
2021-06-09 Fixes nutlock bug in motor brackets
    [motor_bracket_A.stl, motor_bracket_B.stl, motor_bracket_C.stl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]
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2021-06-28 Adds preventor edges to line roller double
    [line_roller_double.scad, line_roller_double.stl]
2021-06-30 Swaps back mixed up B/C motors
    [layout.dxf, layout.scad, motor_bracket_B.scad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]
2021-06-30 Cosmetic fixes in layout file
    [layout.scad]
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2021-07-12 Improves tolerances and encloses line path more
    It was found during testing that the line was not kep well enough
    in place by the spool cover and GT2 spool gear.
    [GT2_spool_gear.scad, dleft_spool_cover.scad, dleft_spool_cover.stl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]
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2021-07-13 Tighter tolerance for GT2 spool gear
    [GT2_spool_gear.scad]
2021-07-13 Improves tolerances
    Achieved by
    - Merging motor bracket and spool core/legs into one part
    - Adding and subtracting 0.2 mm here and there, based on
    experience from practical testing.
    [dleft_spool.stl, dleft_spool_cover.stl, layout.scad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]
2021-07-14 Fixes minor bug in motor bracket D
    [motor_bracket_D.stl]
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2021-08-16 Gives spool outer disc 1 mm more radius
    This harmonizes the GT2_spool_gear outer radius (including its flange)
    with the sep disc (aka spool outer disc) radius.
    Which means we can now fit a bit more line on the spool, and it's
    easier to mount the spool sandwich perfectly, without scraping
    between spool/spool gear and cover.
    [GT2_spool_gear.scad, dleft_spool.stl, dleft_spool_cover.stl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]
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2021-08-16 Revert "Makes more space for the belt"
    This reverts commit 2f493cda1c66f11c68d05d3d5514b58c19ae3602.
    [dleft_spool_cover.stl, spool_cover.scad, spool_cover.stl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]
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2021-08-19 Changes directions of all motors
    This is necessary because we changed the CAN addresses in an earlier
    commit.
    Turns out that CAN address change made all motors go backwards when they
    were supposed to go forwards, and vice versa.
    [config.g]
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2021-08-25 Adds spacers to 1XD_holder
    We had one incidence of not using spacers.
    The 1XD board bent slightly and actually broke.
    [1XD_holder.scad, 1XD_holder.stl]
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2021-08-27 Minor changes to brace tightener
    [brace_tightener.scad, brace_tightener.stl]
2021-08-30 More conservative accel/jerk config
    We observed that infill did not always adhere to perimeters,
    causing holes in prints when viewed from above.
    By setting lower accelerations and jerks in the ABC/XY directions,
    these holes were eliminated.
    [config.g]
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2021-09-01 Makes three more line roller anchor options
    Also makes more room for the line.
    We observed that lines were eaten up, and also twisted and therefore
    shortened during print, by line rollers that had the wrong tilt angle.
    [line_roller_anchor.scad, line_roller_anchor_half_tilt.scad, line_roller_anchor_half_tilt.stl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]
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2021-09-14 Converts tilted line deflector to 608 bearing
    This is because we've seen some fraying of the lines
    that rolled over the old version, that used a smaller
    623 bearing.
    [bearing_u_608.scad, bearing_v_608.scad, horizontal_line_deflector.scad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]
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2021-10-05 Fix for line squeeze bug
    [tilted_line_deflector.scad, tilted_line_deflector.stl, tilted_line_deflector_mirrored.stl]
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2021-10-13 Yet another tilted line deflector fix
    [tilted_line_deflector.scad, tilted_line_deflector.stl, tilted_line_deflector_mirrored.stl]
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2021-10-18 Extends dspool for wire rewinding
    ... only thing missing is the dright spool cover,
    which is not made yet.
    [dright_spool_bottom.scad, dright_spool_bottom.stl, dright_spool_top.scad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]
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2021-10-19 Adds line roller wire rewinder
    Note: Not integrated into layout.scad.
    So layout_a4.pdf is not up to date yet.
    Makefile is also missing every stl that has to do with wire rewinding.
    [line_roller_double.scad, line_roller_wire_rewinder.scad, line_roller_wire_rewinder.stl]
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2021-10-21 Improves tolerances for dright spool bearing
    [dright_spool_bottom.scad, dright_spool_bottom.stl]
2021-10-22 Prevents bearing from falling into dright spool bottom
    [dright_spool_bottom.scad, dright_spool_bottom.stl, spool.scad]
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2021-11-01 Changes velocity limits on the ODrives
    The old 180000 counts/s value is replaced with the new value
    180000/2400 = 75 rev/s
    The old value were found by speeding up motors until plastic parts
    started to vibrate badly.
    While doing that test, I had encoders with 2400 counts per revolution.
    [configure_odrive.py]
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2021-11-01 Fixes vel limit bug
    Also explains the accel and decel limits better
    [configure_odrive.py]
2021-11-06 Adds pen holder
    Heavily inspired by Tech2C's 1_Axis_Pen_Holder.stl found here:
    https://www.thingiverse.com/thing:2459624/files
    Re-implemented in Openscad.
    Doubled y-length and added Nema17 attachment to match Hangprinter
    bracket.
    Adds studs at bottom to help adjust rubber band length, and to stabilize
    Hangprinter mount.
    [pen_holder_moving_part.scad, pen_holder_moving_part.stl, pen_holder_nut_head.scad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]
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2021-11-16 Makes brace tightener a bit more practical
    [brace_tightener.scad, brace_tightener.stl]
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2021-12-07 Fixes tilted line deflector
    [tilted_line_deflector.scad, tilted_line_deflector.stl, tilted_line_deflector_mirrored.stl]
2021-12-07 Fixes mirrored line deflector angle
    [tilted_line_deflector.scad, tilted_line_deflector_mirrored.scad, tilted_line_deflector_mirrored.stl]
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2022-01-20 Increases segments per second
    This avoids slack in the lines during travel moves
    [config.g]
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2022-01-27 Fixes fly brace angles
    [pen_fly_brace.scad, pen_fly_brace.stl]
2022-01-29 fixes typo
    [tilted_line_deflector.scad]
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2022-02-22 Reverts shortening of pi_mount
    [pi_mount.scad, pi_mount.stl]
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2022-03-14 Improves support for flex compensation
    [config.g]
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2022-03-15 More flex comp config changes
    [config.g]
2022-03-15 New flex compensating fw binary
    [config.g]
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2022-03-17 Revert "Upgrades default ODriveFirmware to 0.5.4"
    This reverts commit 0052bc2e90c143b63b2291ed234a22992207e328.
    [odrive-config-AB.json, odrive-config-CD.json]
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2022-05-20 Removes double brace tightener from repo
    [double_brace_tightener.scad, double_brace_tightener.stl]
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2022-09-21 Adds missing stls
    [clay_extruder.stl, clay_extruder_holder.stl, spool_mirrored.stl]
2022-09-21 Minor bug in layout rendering
    [layout.scad]
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2022-09-21 Fixes bug in configure_odrive.py
    [configure_odrive.py]
2022-12-19 Fixes mirroring of dright_spool_top.stl
    [dright_spool_top.scad, dright_spool_top.stl, layout.scad]
2023-06-05 Renames clay extruder to ram_1000_3dpotter
    ... and also fixes some minor bugs and missing stl files.
    [clay_extruder_holder.scad, layout.scad, ram_1000_3dpotter.scad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]
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
